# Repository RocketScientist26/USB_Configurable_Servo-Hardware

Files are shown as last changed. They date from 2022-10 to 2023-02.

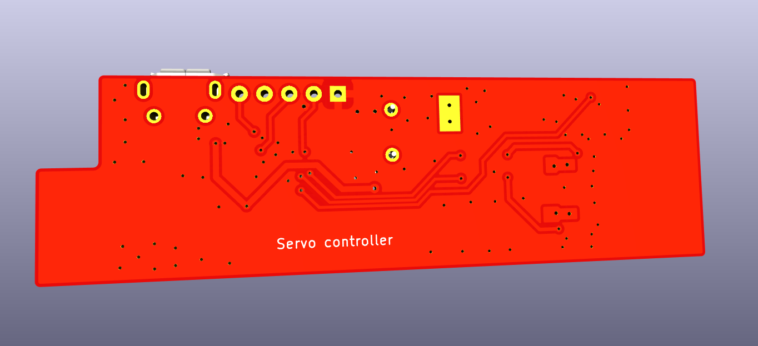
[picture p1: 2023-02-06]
Servo_Controller/Docs/PCB Bottom.png

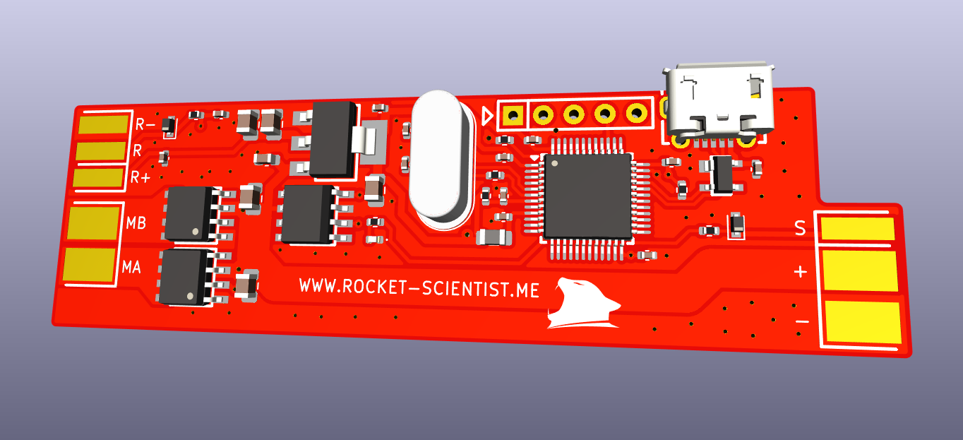
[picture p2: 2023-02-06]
Servo_Controller/Docs/PCB Top.png

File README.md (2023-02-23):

# USB Configurable Servo - Hardware

Open source servo motor brain, intended for lab tests and development.

Project page: [https://rocket-scientist.me/servo.html](https://rocket-scientist.me/servo.html)

- Built from vastly available cheap electronic components
- Fully configurable via USB
- Realtime monitoring from Qt app with graphs and controls
- Can be used with ready made cheap mechanical parts, or with your own designs
- Code kept as clean and simple as possible

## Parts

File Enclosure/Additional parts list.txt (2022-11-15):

- 3Pcs, 6mm length, round head (Phillips), M2 screws
- 3Pcs, 4mm depth, M2 screw mount insets
- 1Pcs, 5mm length, 1.7mm diameter, transparent, PET or similar, 3D printer filament chunk (for LED hole, mount with soldering iron)

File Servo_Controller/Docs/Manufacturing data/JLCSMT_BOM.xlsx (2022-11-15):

Comment | Designator | Footprint | JLCPCB Part #（optional）
100nf | C1,C2,C3,C6,C7,C8,C9,C14,C15,C16 | SMD_0402 | C110251
20pf | C4,C5 | SMD_0402 | C1554
1uf | C10 | SMD_0603 | C59302
10uf | C11,C12,C13,C17,C18 | SMD_0805 | C95841
PESD5Z5.0.115 | D2 | SOD-523 | C521907
PESD5Z3.3.115 | D3 | SOD-523 | C2892515
Orange LED | D5 | SMD_0402 | C401113
FerriteBead 600 Ohms at 100Mhz | FB1 | SMD_0805 | C98308
USB_Micro-B_Molex-105017-0001 | J1 | SMD_Molex | C132563
4.7k | R2,R3 | SMD_0402 | C304616
1k | R4 | SMD_0402 | C226166
270 Ohms | R5 | SMD_0402 | C25099
390 Ohms | R6 | SMD_0402 | C137997
100 Ohms | R7 | SMD_0402 | C25076
1.5k | R8 | SMD_0402 | C114759
STM32F103CBT6 | U1 | LQFP-48 | C8304
TPD2E001DZDR | U2 | DZD | C89411
AMS1117-3.3 | U3 | SOT-223 | C6186
IRS4427S | U4 | SOIC8N | C171650
AO4616 | U5,U6 | SOIC8 | C115831
Crystal 8Mhz/18pf | Y1 | HC-49_US | C258976

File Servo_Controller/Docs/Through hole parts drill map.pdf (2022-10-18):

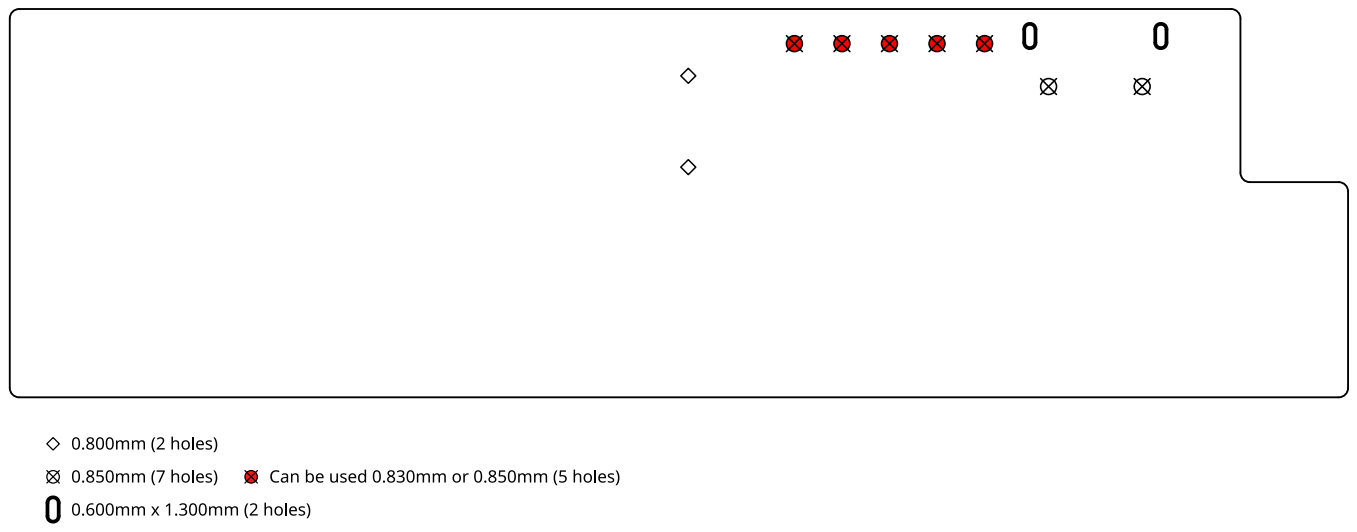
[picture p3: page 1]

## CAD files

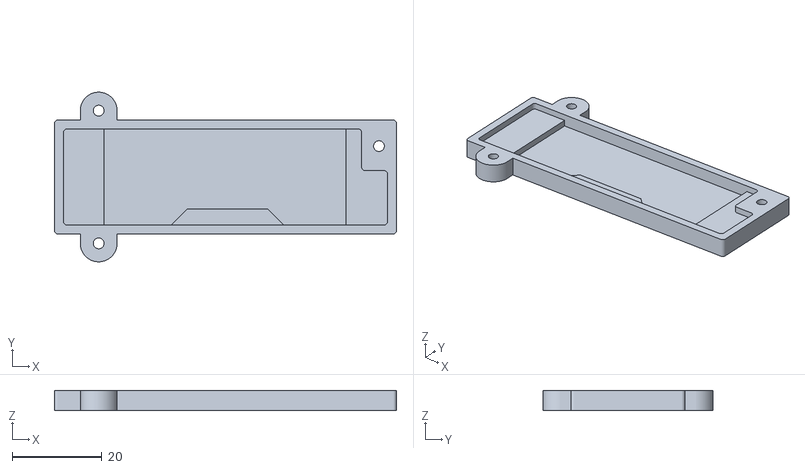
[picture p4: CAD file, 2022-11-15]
Enclosure/Base.stl
76.1 x 37.7 x 4.50

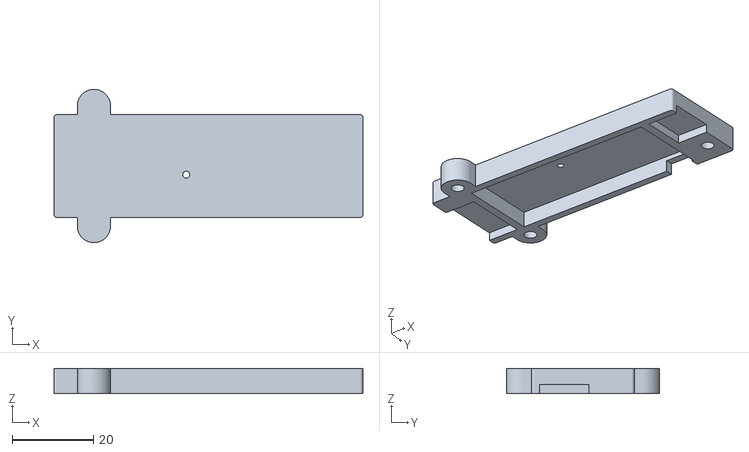
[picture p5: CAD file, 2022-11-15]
Enclosure/Cover.stl
76.1 x 37.7 x 6.20

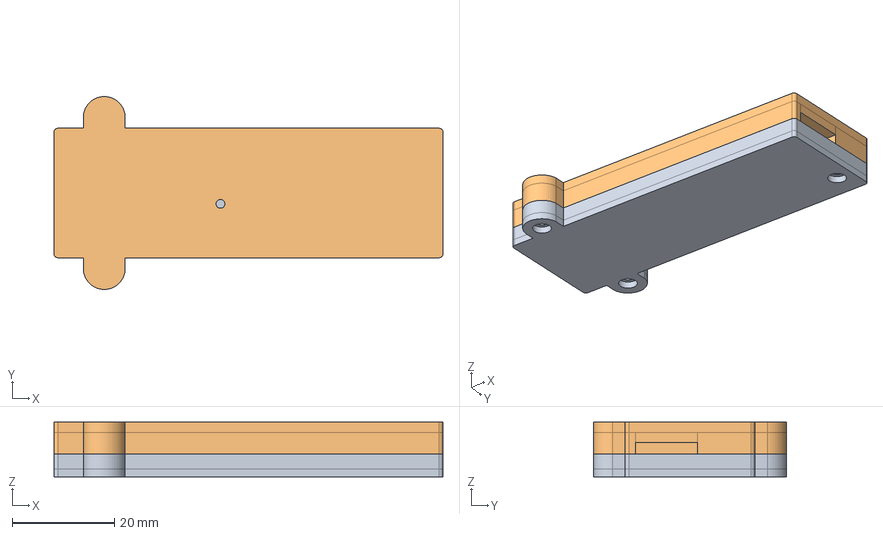
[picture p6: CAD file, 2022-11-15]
Enclosure/Servo_Controller_Enclosure.FCStd
76.1 x 37.8 x 10.7 mm
Base
Cover

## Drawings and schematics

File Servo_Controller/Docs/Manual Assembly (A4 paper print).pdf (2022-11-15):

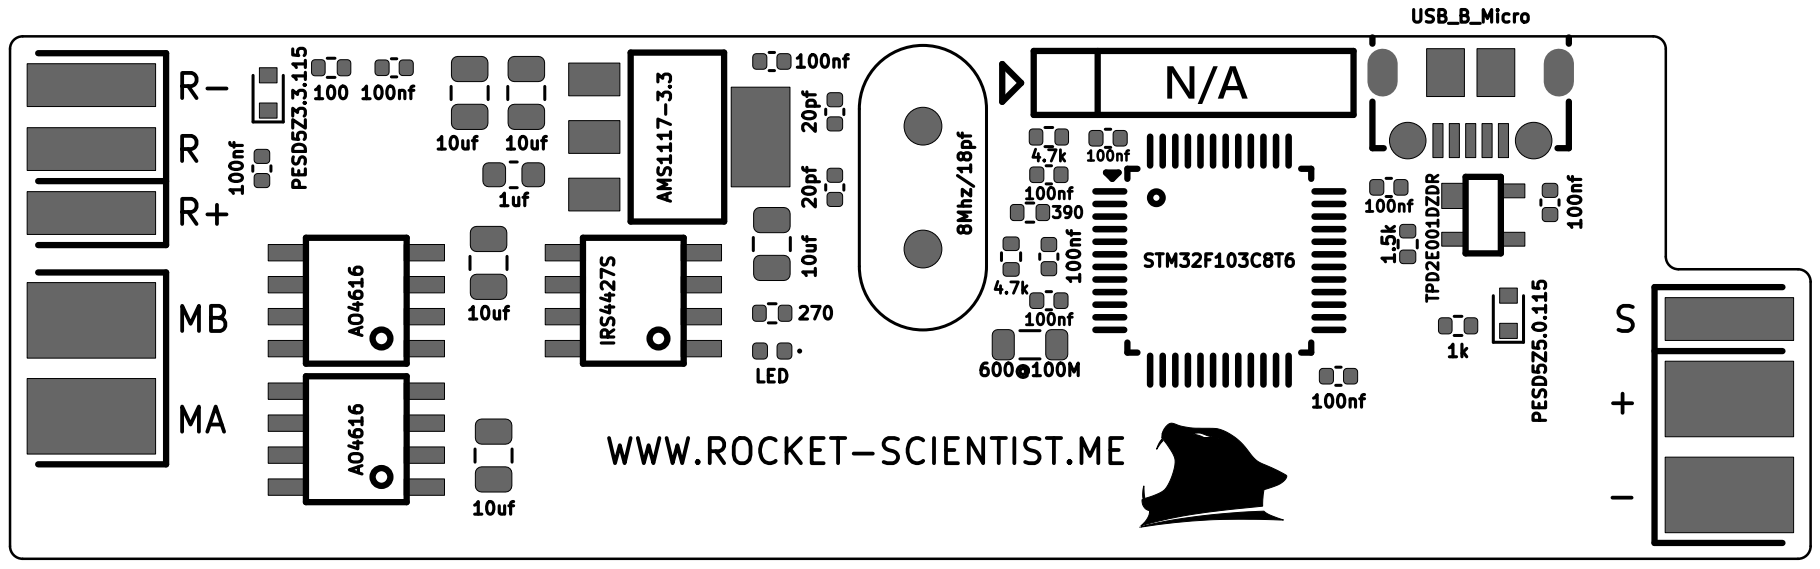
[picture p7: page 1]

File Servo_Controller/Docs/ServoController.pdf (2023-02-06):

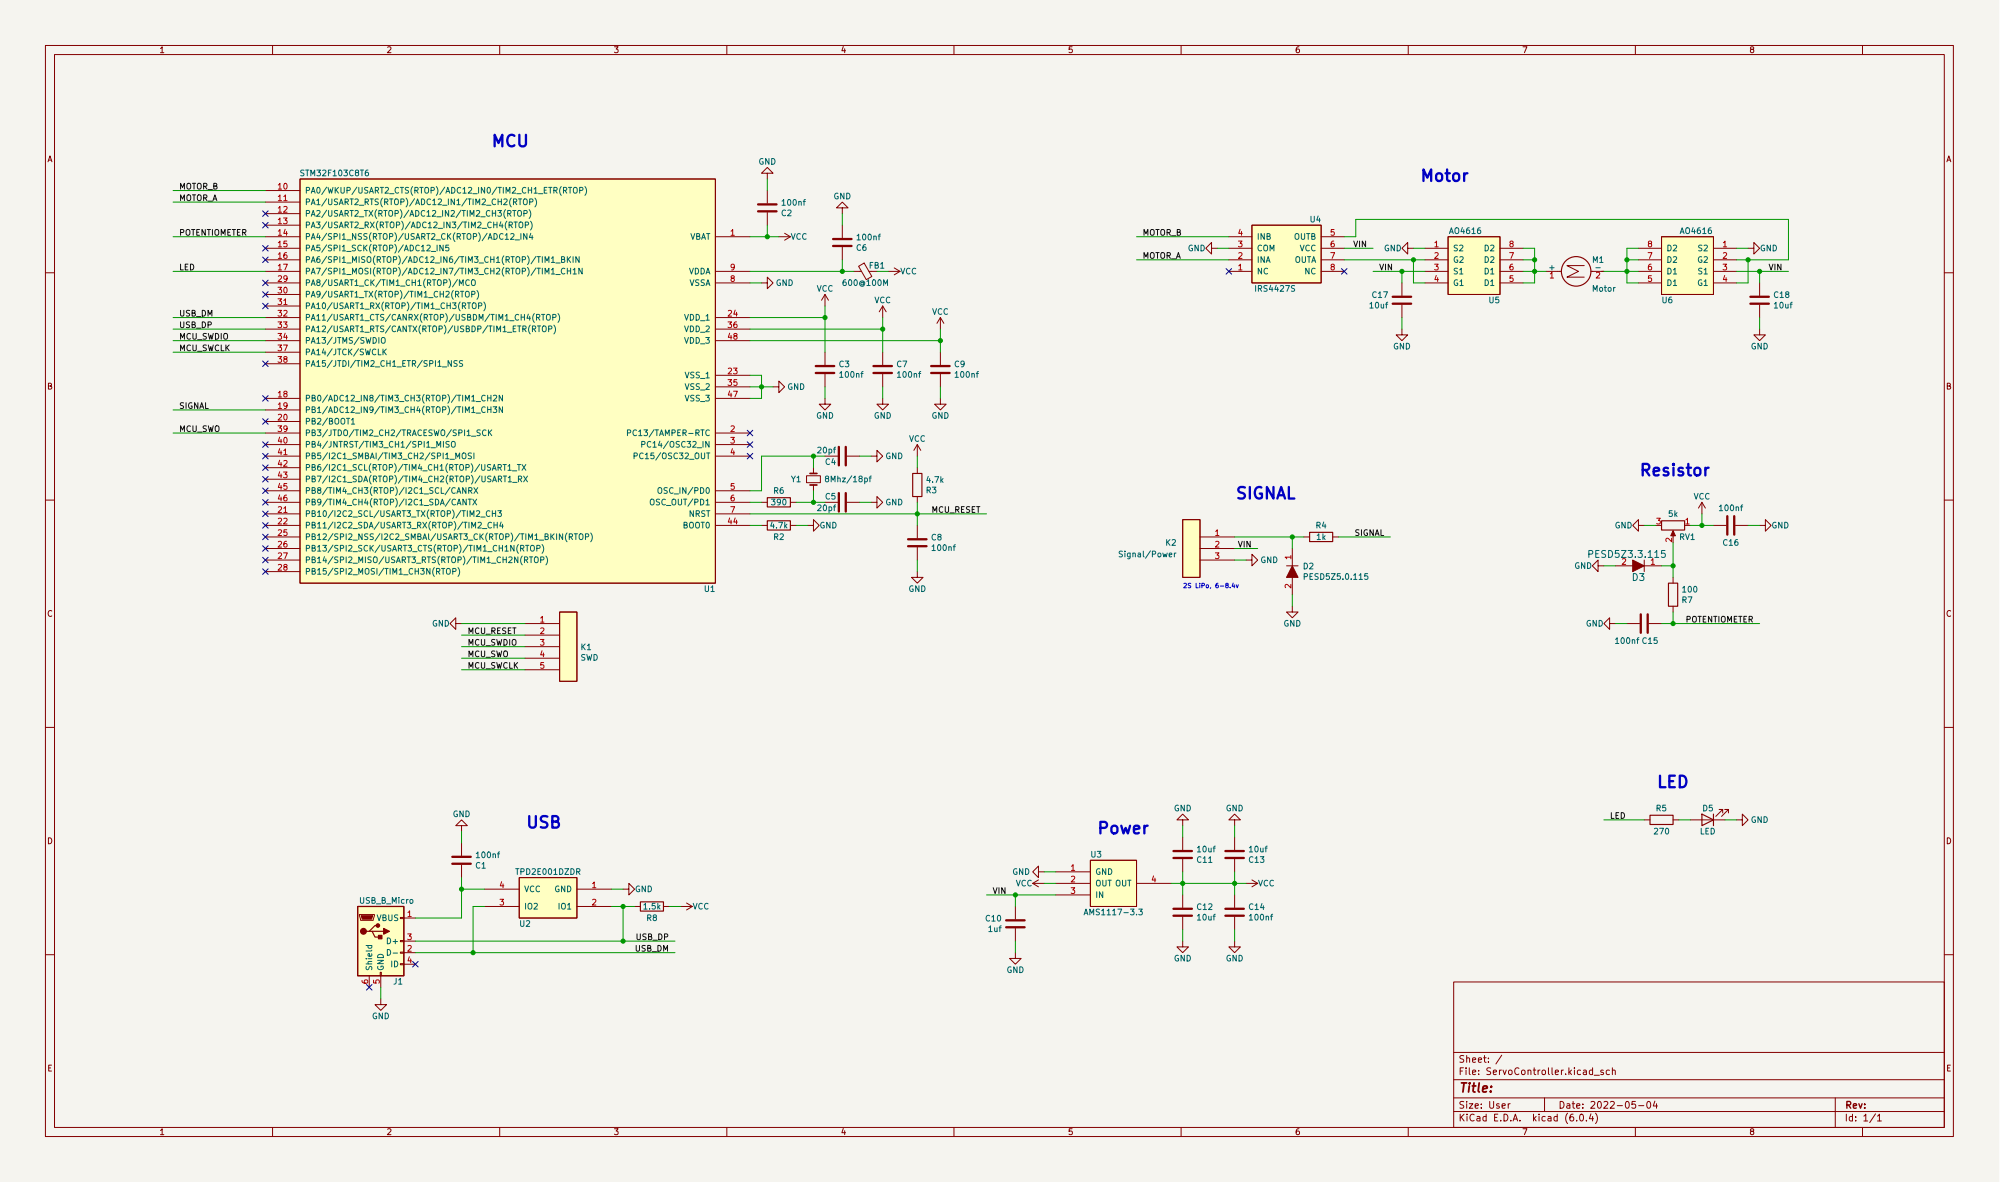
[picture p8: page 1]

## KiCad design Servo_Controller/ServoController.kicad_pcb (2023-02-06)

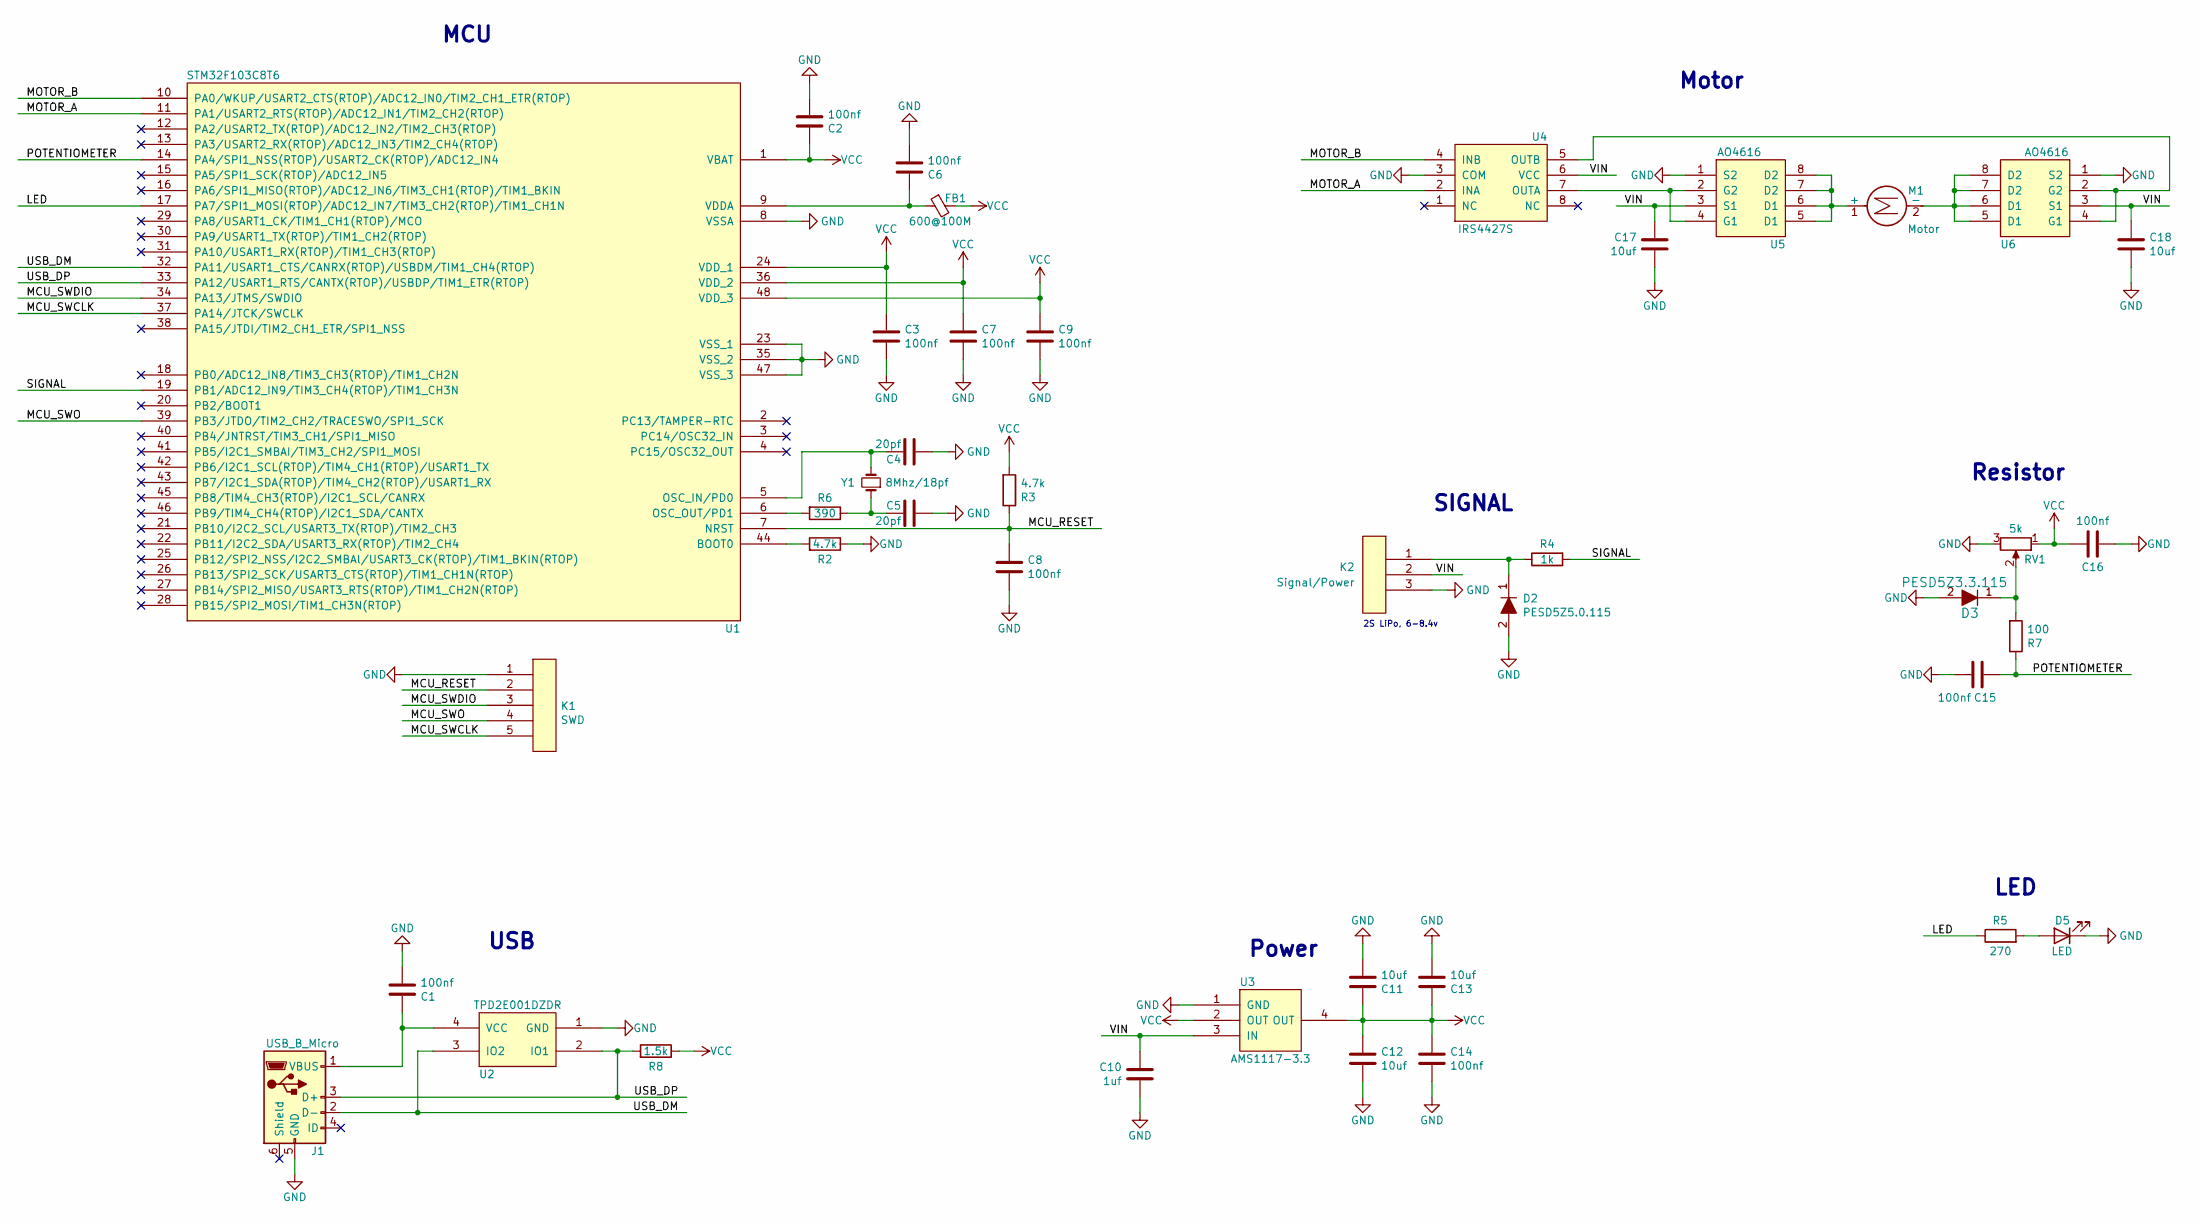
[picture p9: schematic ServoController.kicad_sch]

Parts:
C1, C2, C3, C6, C7, C8, C9, C14, C15, C16: 100nf; C_0402
C4, C5: 20pf; C_0402
C10: 1uf; C_0603
C11, C12, C13, C17, C18: 10uf; C_0805
D2: PESD5Z5.0.115; D_SOD-523
D3: PESD5Z3.3.115; D_SOD-523
D5: LED; LED_0402
FB1: 600@100M; L_0805
J1: USB_B_Micro; USB_Micro-B_Molex-105017-0001
K1: SWD
K2: Signal/Power; Signal_Power
M1: Motor
R2, R3: 4.7k; R_0402
R4: 1k; R_0402
R5: 270; R_0402
R6: 390; R_0402
R7: 100; R_0402
R8: 1.5k; R_0402
RV1: 5k; Potentiometer
U1: STM32F103C8T6; LQFP-48
U2: TPD2E001DZDR; DZD
U3: AMS1117-3.3; SOT-223
U4: IRS4427S; SOIC8N
U5, U6: AO4616; SOIC-8
Y1: 8Mhz/18pf; HC-49_US

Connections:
/LED: R5.1, U1.17 (PA7/SPI1_MOSI(RTOP)/ADC12_IN7/TIM3_CH2(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)
/MCU_RESET: C8.1, K1.2, R3.1, U1.7 (NRST)
/MCU_SWCLK: K1.5, U1.37 (PA14/JTCK/SWCLK)
/MCU_SWDIO: K1.3, U1.34 (PA13/JTMS/SWDIO)
/MCU_SWO: K1.4, U1.39 (PB3/JTDO/TIM2_CH2/TRACESWO/SPI1_SCK)
/MOTOR_A: U1.11 (PA1/USART2_RTS(RTOP)/ADC12_IN1/TIM2_CH2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), U4.2 (INA)
/MOTOR_B: U1.10 (PA0/WKUP/USART2_CTS(RTOP)/ADC12_IN0/TIM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), U4.4 (INB)
/POTENTIOMETER: C15.1, R7.1, U1.14 (PA4/SPI1_NSS(RTOP)/USART2_CK(RTOP)/ADC1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)
/SIGNAL: R4.2, U1.19 (PB1/ADC12_IN9/TIM3_CH4(RTOP)/TIM1_CH3N)
/USB_DM: J1.2 (D-), U1.32 (PA11/USART1_CTS/CANRX(RTOP)/USBDM/TIM1_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), U2.3 (IO2)
/USB_DP: J1.3 (D+), R8.2, U1.33 (PA12/USART1_RTS/CANTX(RTOP)/USBDP/TIM1_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), U2.2 (IO1)
/VIN: C10.1, C17.1, C18.1, K2.2, U3.3 (IN), U4.6 (VCC), U5.3 (S1), U6.3 (S1)
GND: C1.2, C2.2, C3.2, C4.2, C5.2, C6.2, C7.2, C8.2, C9.2, C10.2, C11.2, C12.2, C13.2, C14.2, C15.2, C16.2, C17.2, C18.2, D2.2, D3.2, D5.1 (K), J1.5 (GND), K1.1, K2.3, R2.1, RV1.3, U1.8 (VSSA), U1.23 (VSS_1), U1.35 (VSS_2), U1.47 (VSS_3), U2.1 (GND), U3.1 (GND), U4.3 (COM), U5.1 (S2), U6.1 (S2)
unnamed: C1.1, J1.1 (VBUS), U2.4 (VCC)
unnamed: C4.1, U1.5 (OSC_IN/PD0), Y1.2
unnamed: C5.1, R6.1, Y1.1
unnamed: C6.1, FB1.1, U1.9 (VDDA)
unnamed: D2.1, K2.1, R4.1
unnamed: D3.1, R7.2, RV1.2
unnamed: D5.2 (A), R5.2
unnamed: M1.1 (+), U5.5 (D1), U5.6 (D1), U5.7 (D2), U5.8 (D2)
unnamed: M1.2 (-), U6.5 (D1), U6.6 (D1), U6.7 (D2), U6.8 (D2)
unnamed: R2.2, U1.44 (BOOT0)
unnamed: R6.2, U1.6 (OSC_OUT/PD1)
unnamed: U4.5 (OUTB), U6.2 (G2), U6.4 (G1)
unnamed: U4.7 (OUTA), U5.2 (G2), U5.4 (G1)
VCC: C2.1, C3.1, C7.1, C9.1, C11.1, C12.1, C13.1, C14.1, C16.1, FB1.2, R3.2, R8.1, RV1.1, U1.1 (VBAT), U1.24 (VDD_1), U1.36 (VDD_2), U1.48 (VDD_3), U3.2 (OUT), U3.4 (OUT)

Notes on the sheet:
Motor
Resistor
LED
MCU
SIGNAL
USB
Power
2S LiPo, 6-8.4v

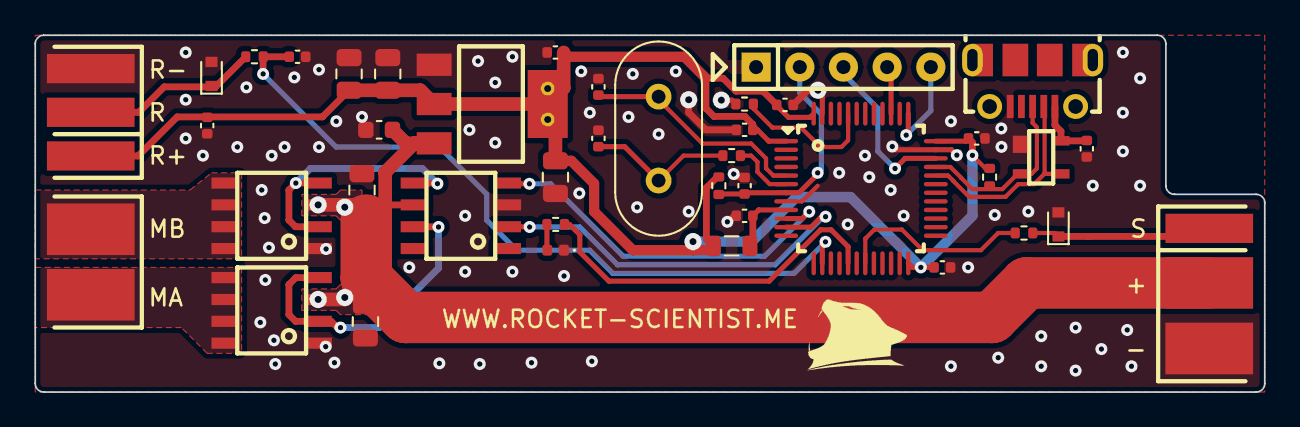
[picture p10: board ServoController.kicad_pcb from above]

Board: 2 copper layers, 71.5 x 20.8 mm, 42 parts (0 on the bottom side), 27 nets.

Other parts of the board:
VAL: REF; Logo

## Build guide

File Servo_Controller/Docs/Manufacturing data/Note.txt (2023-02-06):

As of 6 february 2023 commit, JLCPCB assembly service for now is not working.
JLCPCB PCB renders itself are valid for previous commit, parts placements render on them, placement and BOM files have not been changed.

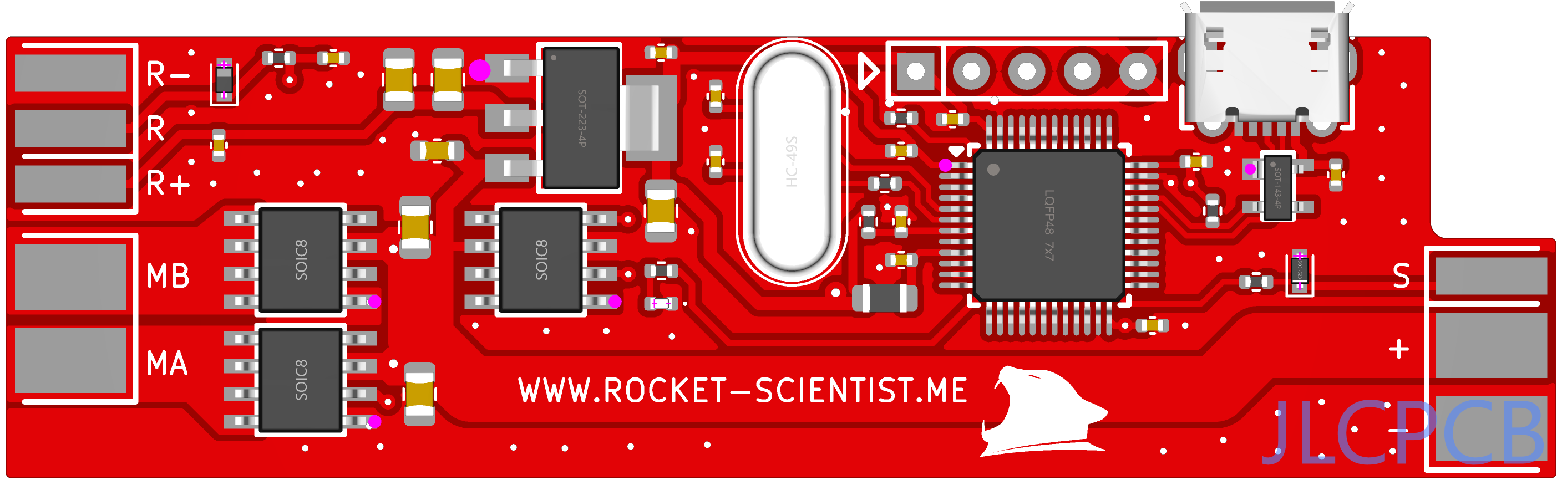
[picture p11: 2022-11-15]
Servo_Controller/Docs/Manufacturing data/JLCPCB Render Top.png

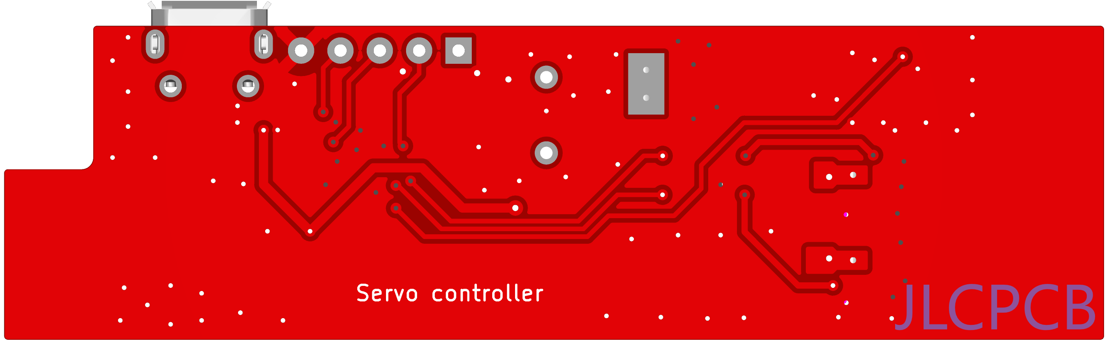
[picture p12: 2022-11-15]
Servo_Controller/Docs/Manufacturing data/JLCPCB Render Bottom.png

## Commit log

2022-05-04 Files upload
    [ServoController-B_Cu.gbl, ServoController-B_Mask.gbs, ServoController-B_Paste.gbp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]
2022-10-18 Manufacturing data added
    [JLCSMT_BOM.xlsx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]
2022-10-23 Manual assembly PDF added, value/reference sizes changed in PCB
    [ServoController.kicad_pcb]
2022-11-15 Added enclosure, removed unnecessary resistor
    [Base.stl, Cover.stl, JLCSMT_BOM.xlsx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]
2023-02-06 Changed VCC to SWO signal on SWD header. Manufacturing data and PCB previews updated
    [ServoController-B_Cu.gbl, ServoController-B_Mask.gbs, ServoController-B_Paste.gbp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]
